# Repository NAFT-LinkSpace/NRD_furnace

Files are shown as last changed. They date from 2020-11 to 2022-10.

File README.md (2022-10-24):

# 温度制御用炉の電装

- 温度制御ができる(PID 制御)
- 設定すれば何でも暖かくできる
- CFRP 加熱成形用として開発した

## 利用したもの

- Arduino Uno
- Arduino Uno 用シールド用ユニバーサル基板(<https://akizukidenshi.com/catalog/g/gP-06877/>)
- K 型熱電対 ×3
- 熱電対モジュール(MAX31855) ×3
- ソリッド・ステート・リレー（ＳＳＲ）キット(<https://akizukidenshi.com/catalog/g/gK-00203/>)
- 延長コード等

## 環境

- PlatformIO

## 使用法

詳細はそれぞれの項目を参照

- 制御対象のステップ応答から制御対象の時定数と遅れ時間とゲインを得る。
- シミュレーションのコードに定数を代入して実行すると PID ゲインが得られる。
- 制御に必要なパラメータを設定する。
- PlatformIO で Arduino Uno に書き込む。
- UART でコマンドを送れば制御開始
- duty 比一定の出力も可能
- T0,T1,T2 は 3 つの熱電対で測定するそれぞれの温度(3 つ以下でも動く)

## 制御目標の設定

[制御設定用ファイル](code/src/control_parameter.hpp)の関数 targetFunction を与えると設定できる。

- 例

  | 時刻[min] | 温度[℃] |
  | --------- | ------- |
  | 0         | 20      |
  | 20        | 40      |
  | 30        | 40      |
  | 50        | 20      |

  - 表のような温度変化を関数で表すと以下のコードのようになる。
  - inflectionPoint は直線で目標の関数を与えるときの変曲点(角)を示す。時間と温度を代入する。
  - 制御終了は`is_end = true`で可能

    ```c++
        struct inflectionPoint {
            double time_s;
            double temp_cels;
        };
        static constexpr inflectionPoint inflectionpoint_s[] = {{0, 20}, {20 * 60, 40}, {30 * 60, 40}, {50 * 60, 20}};

        inline double targetFunction(const double elapsed_time_s, bool& is_end) {
            is_end = false;
            if (elapsed_time_s < inflectionpoint_s[0].time_s) {
                return 0;
            }
            if (elapsed_time_s < inflectionpoint_s[1].time_s) {
                return linear(inflectionpoint_s[0], inflectionpoint_s[1], elapsed_time_s);
            }
            if (elapsed_time_s < inflectionpoint_s[2].time_s) {
                return linear(inflectionpoint_s[1], inflectionpoint_s[2], elapsed_time_s);
            }
            if (elapsed_time_s < inflectionpoint_s[3].time_s) {
                return linear(inflectionpoint_s[2], inflectionpoint_s[3], elapsed_time_s);
            }

            is_end = true;
            return 0.0;
        }

    ```

## フィードバック対象の設定

[制御設定用ファイル](code/src/control_parameter.hpp)の関数 feedbackTemperature を与えると設定できる。

- 例
  ```c++
  inline double feedbackTemperature(const double T0, const double T1, const double T2, const double elasped_time_s) {
      return T1;
      // return (T0 + T1 + T2) / 3;
  }
  ```

## PWM 周期の設定

[制御設定用ファイル](code/src/control_parameter.hpp)の PWM_PERIOD_ms を与えると設定できる。

## シリアル通信

UART(デフォルト 19200bps)で通信。マイコンからは実行時間、温度、状態、状態に応じた情報が送られる。
状態はコマンドによって遷移する。

SET_DUTY で ConstPWM に遷移したとき

```
now_ms:1001, current temp T0:20.3,T1:20.5,T2:0.0,State:ConstPWM, duty[%]:0.0,
```

START_CONTROL で Control に遷移したとき

| elasped  | target | heat out |
| --- | --- | --- |
| 経過時間 | 目標温度 | 実際に出力された熱量 |

```
now_ms:1143003, current temp T0:22.3,T1:23.0,T2:0.0,State:Control, elasped[s]:1.9,e(t):-2.9,target[Cels]:20.1,heat out[W]:152.2,duty[%]:44.7,
```

## コマンドの書式

### コマンド コマンド引数 改行コード(CRLF or LF)

[コマンド設定用ファイル](code/src/keyword.hpp)にあるコマンドをシリアル通信で送れば操作できる。

| コマンドの変数名 | コマンドのデフォルト値 | 引数の型(C/C++) | 引数の範囲 | 引数の単位 | 内容 | 内部状態 |
| --- | --- | --- | --- | --- | --- | --- |
| SET_DUTY | 1 | float | 0~100 | % | 引数で指定した duty 比を出力する | ConstPWM へ |
| START_CONTROL | 2 | float | 0 以上 (省略した場合 0 ) | second | 引数で指定した時間だけ経過時間を進めてから制御を開始する | Control へ  |

例 コマンドのデフォルト値のとき

- duty 比 20%で出力

  ```
  1 20
  ```

- 経過時間 0 秒から制御開始

  ```
  2
  ```

  もしくは

  ```
  2 0
  ```

- 経過時間 100 秒から制御再開(プログラムが止まったりしたときに途中から再開できる)
  ```
  2 100
  ```

## 回路

熱電対を接続し制御対象の温度を測定する。
SSR に繋がったフォトトライアックに PWM を入力し電熱線で制御対象を加熱する。[ピン設定用ファイル](code/src/pin.hpp)で熱電対センサの SPI と PWM 出力のピンアサインを変更可能。

## 設計

制御方法やその他

### シミュレーション

matplotlib,numpy,python control に依存したシミュレーションコード。
制御対象のステップ応答から PID ゲインを求めて matplotlib で温度-時間,熱量-時間グラフを書いてくれる。

main 関数の一部

```python
  satirated_temperature_cels = 150 # 収束したときの温度
  atmosphere_temperature_cels = 20 # 大気温度

  # 炉の性能
  resistance_ohm = 29.4 # 電熱線の抵抗値
  L_delayed_s = 51  # 遅れ時間
  temp_tau_s = 2000  # 1次遅れの時定数
  tau_s = temp_tau_s  # 時定数

  input_to_system_W = 100 ** 2 / resistance_ohm # 炉への最大熱量出力

```

実行後のコンソール。以下を[制御設定用ファイル](code/src/control_parameter.hpp)に書き込む。

```
constexpr double MAX_OUTPUT_ENERGY_W = 340.13605442176873 ;
constexpr double Kp = 61.56308677317081 ;
constexpr double Ki = 0.030781543386585404 ;
constexpr double Kd = 1569.8587127158557 ;
```

# 設計

## 制御則

### PID ゲイン設計

[CHR 法](https://ja.wikipedia.org/wiki/PID%E5%88%B6%E5%BE%A1#CHR%E6%B3%95)(オーバーシュート 0%)で設計した。

### 制御器の設計

PID 制御器の実装は速度型 PID で行った。(参考 https://www.nikko-pb.co.jp/products/k_data/P12_13.pdf)
要するに出力に制限があっても(サチっても)ワインドアップしにくい。

## ファームウェア

PlatformIO で開発した Arduino のコード。Arduino Uno 用で開発した。

出力の制御は PWM で実装した。

出力をコントロールするために SSR にフォトトライアックに PWM で信号を送信する。基本的にはデューティ比が出力の熱量と比例するが、利用したフォトトライアックはゼロクロス電力制御が使われているので PWM の周波数は利用する交流電源の周波数より低く設定する必要がある。
~~PFM 制御にしたほうが良かったかもしれないがそうしなかったのは完成するまで気が付かなかったためである。~~

<!-- ### 制御則の設計
1. 制御対象を求める
制御対象を一次遅れ系+無駄時間としてステップ応答を測定した。

PIDゲインを決定した。 -->

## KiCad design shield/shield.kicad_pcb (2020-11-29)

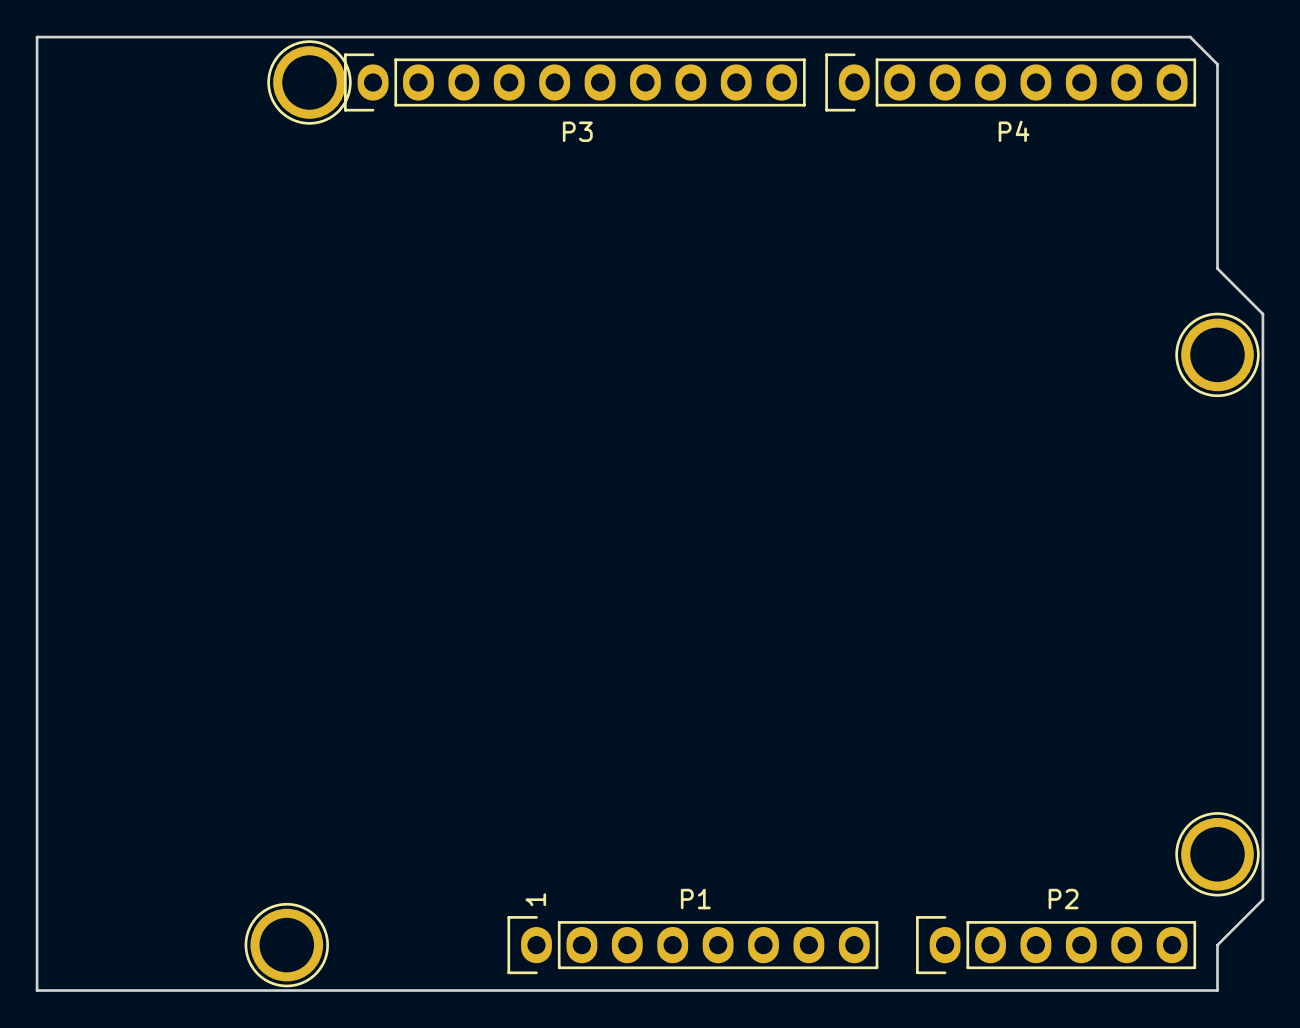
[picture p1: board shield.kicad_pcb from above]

Board: 2 copper layers, 68.6 x 53.3 mm, 8 parts (0 on the bottom side), 3 nets, no tracks yet.

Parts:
P1: Power; Socket_Strip_Arduino_1x08
P2: Analog; Socket_Strip_Arduino_1x06
P3: Digital; Socket_Strip_Arduino_1x10
P4: Digital; Socket_Strip_Arduino_1x08
P5, P6, P7, P8: CONN_01X01; Arduino_1pin

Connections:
/A4(SDA): P2.5, P3.2
/A5(SCL): P2.6, P3.1
GND: P1.6, P1.7, P3.4

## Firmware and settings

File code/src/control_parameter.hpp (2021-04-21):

// custumize file
#if !defined(CONTROL_PARAMETER)
#define CONTROL_PARAMETER

#include <Arduino.h>

constexpr unsigned long PWM_PERIOD_ms = 300;

// PID gain

constexpr double MAX_OUTPUT_ENERGY_W = 340.13605442176873;
constexpr double Kp = 61.56308677317081;
constexpr double Ki = 0.030781543386585404;
constexpr double Kd = 1569.8587127158557;

struct inflectionPoint {
    double time_s;
    double temp_cels;
};

static constexpr inflectionPoint inflectionpoint_s[] = {{0, 20}, {30 * 60, 80}, {60 * 60, 80}, {83 * 60, 125}, {163 * 60, 125}};
static constexpr int inflectionPointSize = sizeof(inflectionpoint_s) / sizeof(inflectionPoint);

inline const double linear(const inflectionPoint pre, const inflectionPoint next, const double etime_s) {
    return (next.temp_cels - pre.temp_cels) / (next.time_s - pre.time_s) * (etime_s - pre.time_s) + pre.temp_cels;
}

inline const double targetFunction(const double elapsed_time_s, bool& is_end) {
    is_end = false;
    if (elapsed_time_s < inflectionpoint_s[0].time_s) {
        return 0.0;
    }
    for (int i = 1; i < inflectionPointSize; i++) {
        if (elapsed_time_s < inflectionpoint_s[i].time_s) {
            return linear(inflectionpoint_s[i - 1], inflectionpoint_s[i], elapsed_time_s);
        }
    }

    is_end = true;
    return 0.0;
}

// test PID control
// inline double feedbackTemperature(const double T0, const double T1, const double T2, const double elasped_time_s) {
//     bool b;
//     return targetFunction(elasped_time_s, b) - 1.0;
// }

inline const double feedbackTemperature(const double T0, const double T1, const double T2, const double elasped_time_s) {
    return T1;
}
#endif  // CONTROL_PARAMETER

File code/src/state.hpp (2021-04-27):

#if !defined(STATE_HEADER_FILE)
#define STATE_HEADER_FILE

#include "PID.hpp"
#include "Stringer.hpp"
#include "container.hpp"
#include "control_parameter.hpp"
#include "pincontrol.hpp"
#include "queue.hpp"
#include "serial.hpp"

class State {
   public:
    State() {
        pinControlBegin();
    }

    virtual void setOutput(const CommonContainer common) = 0;
    virtual const String toString() const = 0;
};

class Control : public State {
   private:
    VelocityPID pid;
    bool is_control_finished = false;
    unsigned long control_start_ms_;
    double skip_time_s_;

   public:
    Control() {
        is_control_finished = false;
        skip_time_s_ = 0.0;
        pid.init();
        pid.setGain(Kp, Ki, Kd);
    }

    void setOutput(const CommonContainer common) override {
        normal_queue.push(toString());

        const double duty_per = dutyPer(common.now_ms, common.current_tempT0, common.current_tempT1, common.current_tempT2);

        normal_queue.push(is_control_finished ? "control is end" : "");
        setLongPeriodPWM(duty_per, PWM_PERIOD_ms, common.now_ms);
    }

    const String toString() const override {
        return toStringHelper("State", "Control");
    }

    void startControl(const unsigned long start_ms, const double skip_time_s) {
        pid.init();
        is_control_finished = false;
        control_start_ms_ = start_ms;
        skip_time_s_ = skip_time_s;
    }

   private:
    const double dutyPer(const unsigned long now_ms, const double T0, const double T1, const double T2) {
        const double elasped_time_s = (now_ms - control_start_ms_) / 1e3 + skip_time_s_;
        const double target_temp = targetFunction(elasped_time_s, is_control_finished);

        if (is_control_finished) {
            return 0.0;
        }
        const double error = target_temp - feedbackTemperature(T0, T1, T2, elasped_time_s);  //error:target - current
        const double out_W = constrain(pid.output(error, elasped_time_s), 0.0, MAX_OUTPUT_ENERGY_W);

        pid.setPreMV(out_W);
        const double duty_per = constrain(out_W / MAX_OUTPUT_ENERGY_W * 100, 0, 100);

        normal_queue.push(
            toStringHelper("elasped[s]", elasped_time_s) +
            toStringHelper("e(t)", error) +
            toStringHelper("target[Cels]", target_temp) +
            toStringHelper("heat out[W]", out_W));

        return duty_per;
    }
};

class ConstPWM : public State {
   private:
    double duty_per_;

   public:
    ConstPWM() {
        duty_per_ = 0.0;
    }
    void setOutput(const CommonContainer common) override {
        setLongPeriodPWM(duty_per_, PWM_PERIOD_ms, common.now_ms);
    }
    void setDuty(const double duty_per) {
        duty_per_ = constrain(duty_per, 0, 100);
    }
    const String toString() const override {
        return toStringHelper("State", "ConstPWM");
    }
};
#endif  // STATE_HEADER_FILE

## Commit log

2020-11-30 read Temperature
2021-02-20 全部入り
2021-02-21 modify using temperature.update function
2021-02-21 print inputContainer
2021-02-22 use tostringhelper & bug fix about elasped time
    [state.hpp]
2021-03-04 change to use Arduino function
2021-03-06 change pinassign for board
2021-03-06 add shield circuit board
    [shield.fzz]
2021-04-05 pid gain change
2021-04-06 コマンドの説明をわかりやすくした
2021-04-20 appropriate using velocity control
2021-04-25 StringQueue for printing text at the suitable time
2021-04-27 fix:print constrained heatout
